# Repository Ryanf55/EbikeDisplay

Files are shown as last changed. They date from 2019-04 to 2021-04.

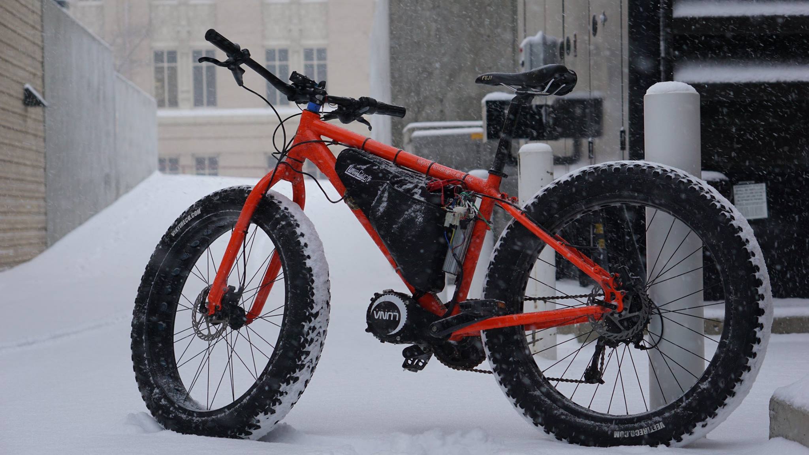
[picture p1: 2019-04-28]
Images/SnowyUse.jpg

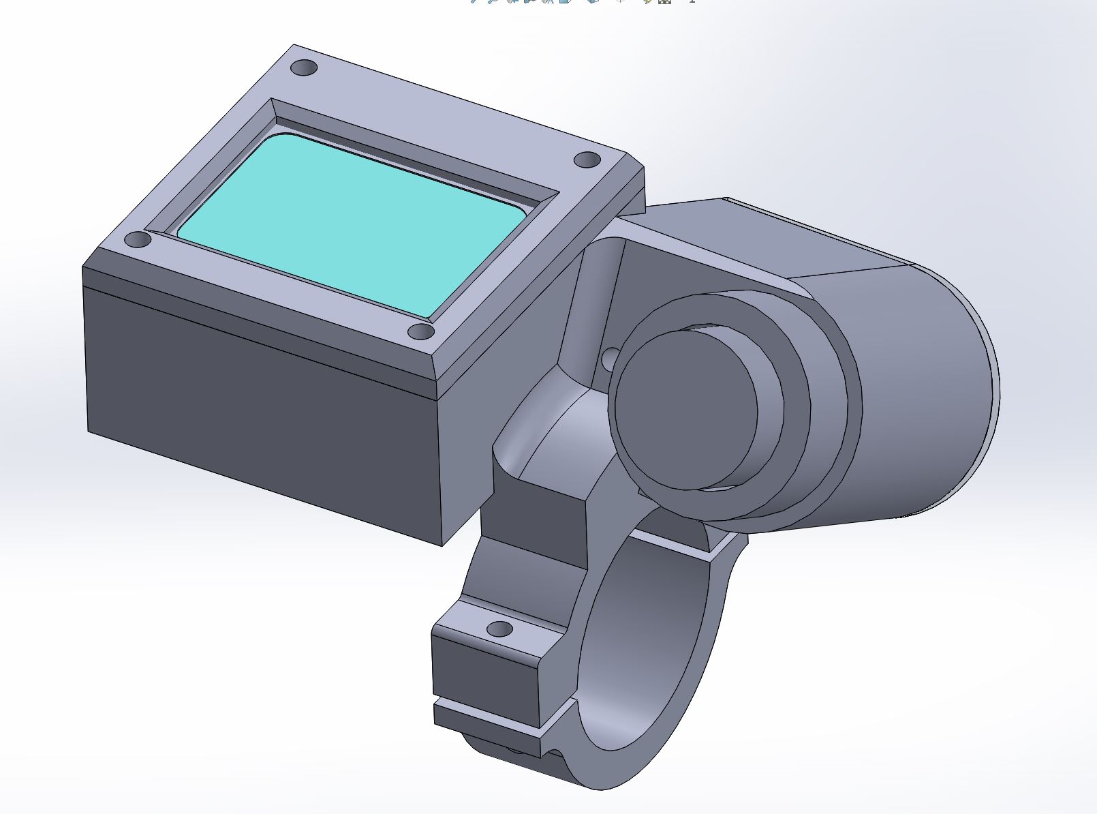
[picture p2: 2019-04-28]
Images/SW1.JPG

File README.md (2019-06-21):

This repo is for an Ebike Controller. It contains a PCB for Nokia 5110 LCD, SolidWorks files / STL's for the case, and Arduino code to work with a cyclone. 

Cyclone throttle cable pinout:
* blue - Vbat 
* black - gnd
* yellow- ignition (connect to Vbat to turn system on)
* green - throttle 0 to 3.3v

stock hall: D49E 503D

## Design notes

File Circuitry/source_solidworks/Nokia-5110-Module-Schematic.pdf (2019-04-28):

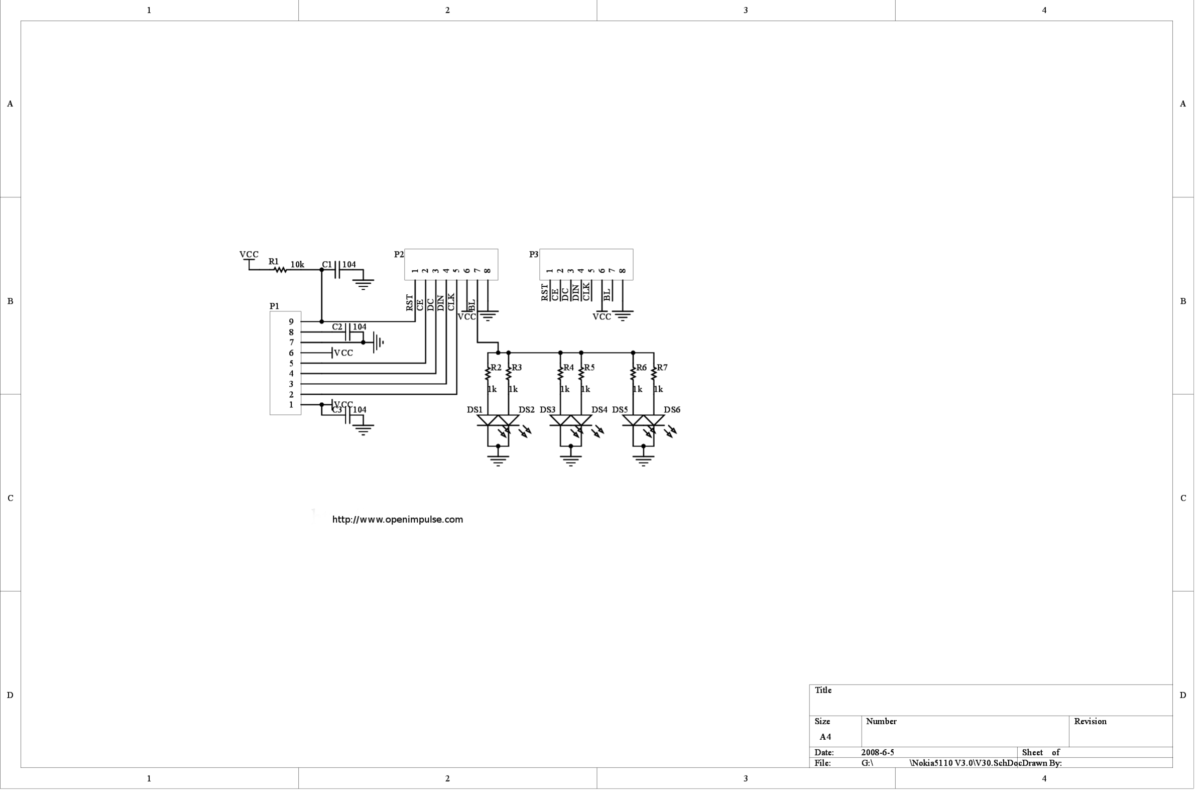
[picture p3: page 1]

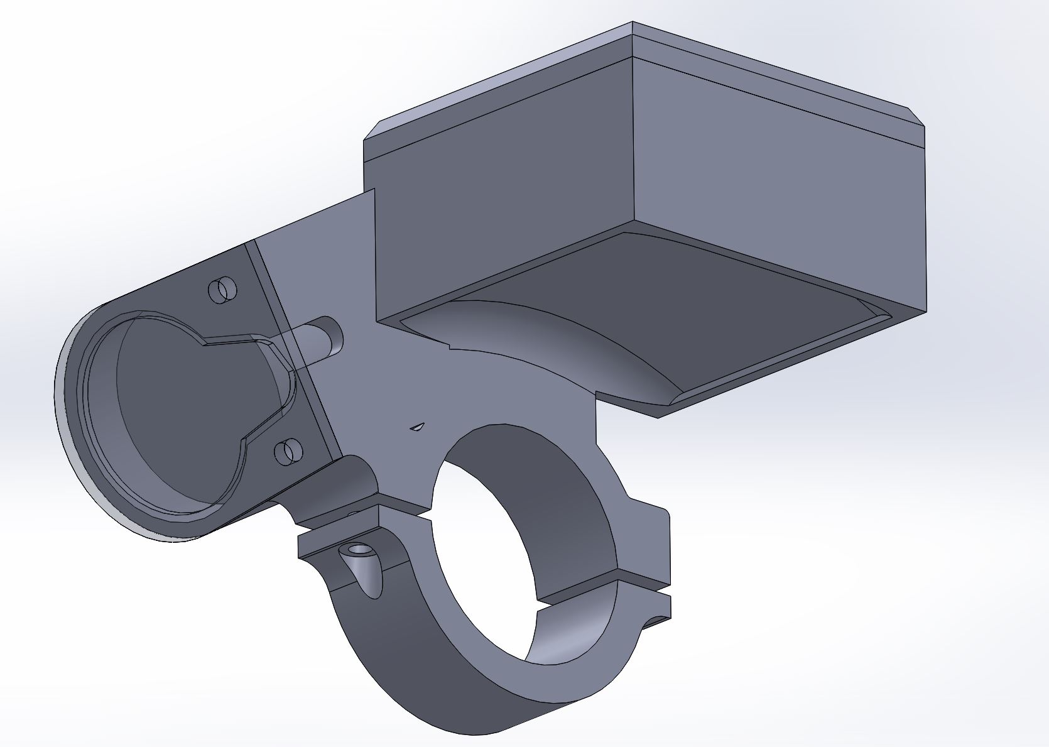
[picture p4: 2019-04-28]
Images/SW2.JPG

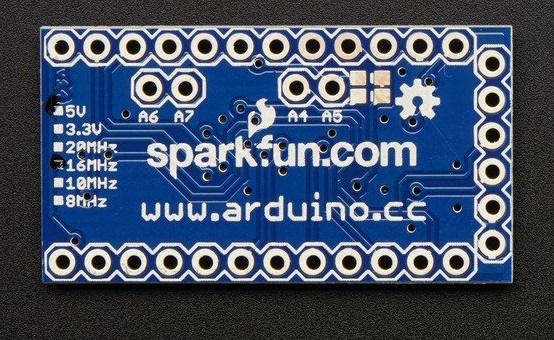
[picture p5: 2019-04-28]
Circuitry/arduino-pro-mini-1.snapshot.9/bot.jpg

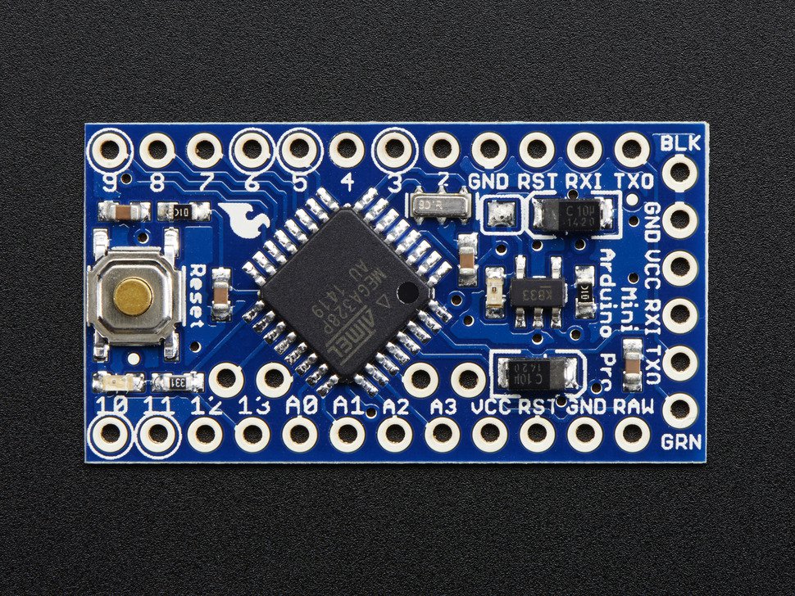
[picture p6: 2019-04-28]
Circuitry/arduino-pro-mini-1.snapshot.9/top.jpg

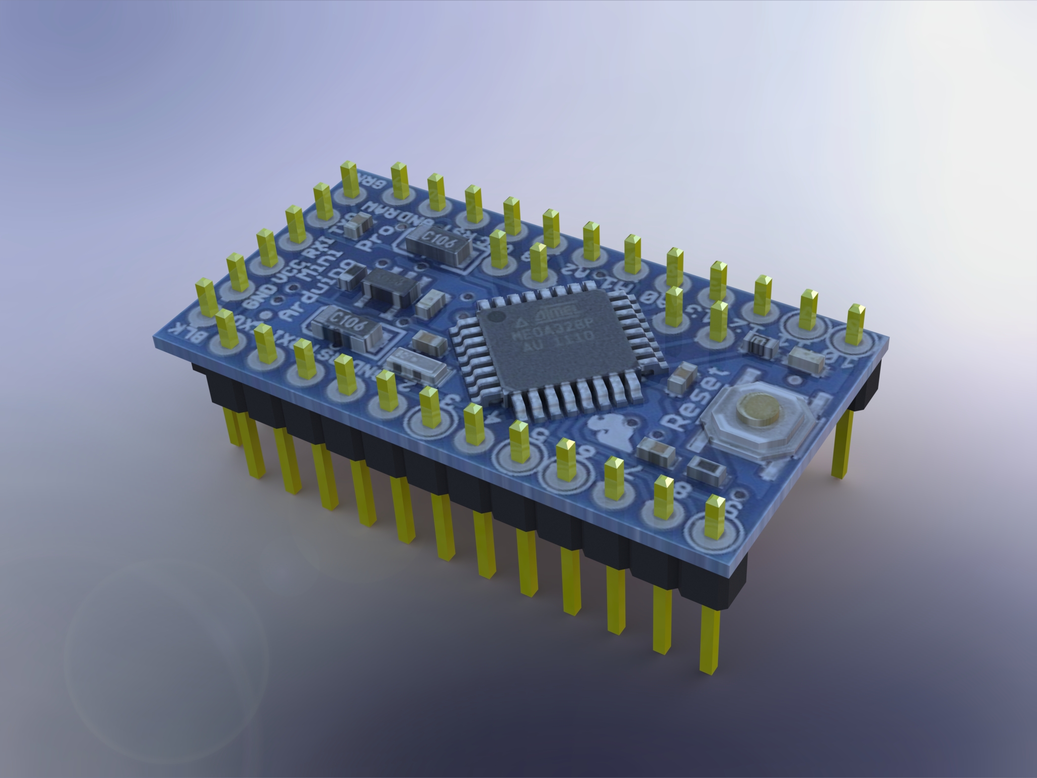
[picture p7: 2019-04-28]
Circuitry/arduino-pro-mini-1.snapshot.9/Renderings/Arduino_pro_mini.JPG

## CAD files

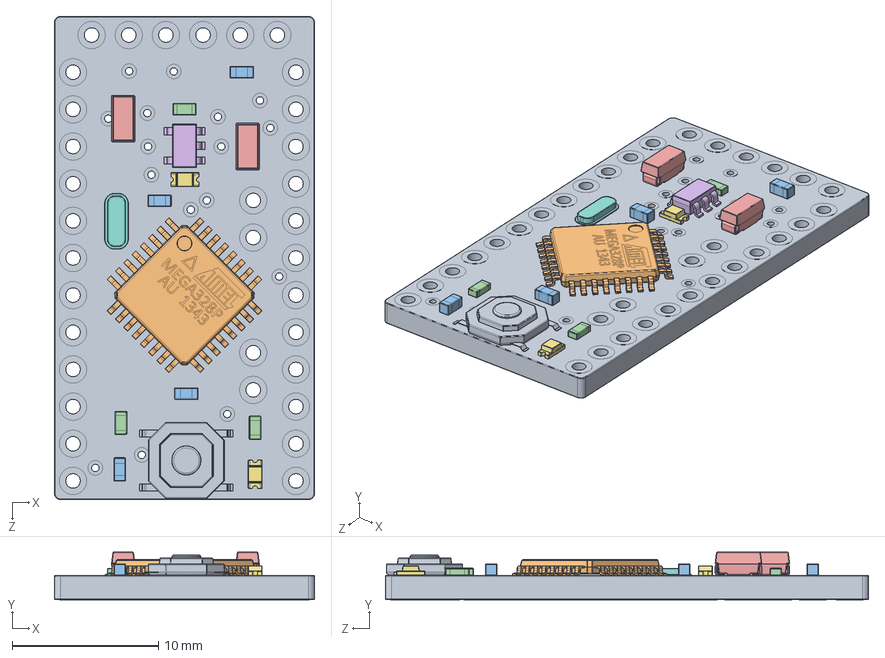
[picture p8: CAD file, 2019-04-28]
Circuitry/arduino-pro-mini-1.snapshot.9/ASSEMBLY.SLDASM
17.8 x 3.26 x 33.0 mm
board
ATmega
cap_603 x 4
res_603 x 3
condensateurTantale_106C x 2
SOT23-5
Surface Mount Chip LED 3.2x1.6mm x 2
TACTILE-SWITCH-SMD-ALT01

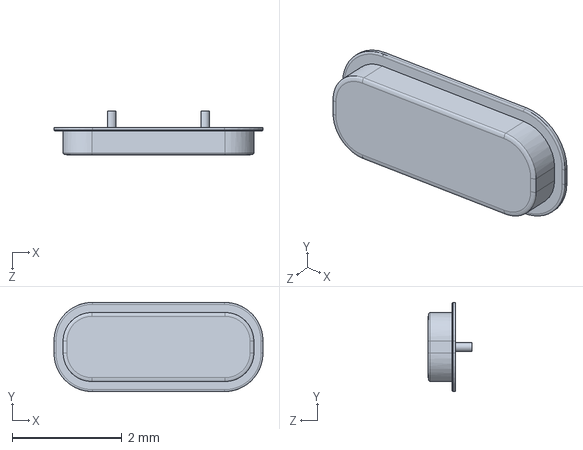
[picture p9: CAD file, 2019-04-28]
Circuitry/arduino-pro-mini-1.snapshot.9/Components/Crystal_Low_Profile.SLDASM
3.82 x 1.63 x 0.795 mm

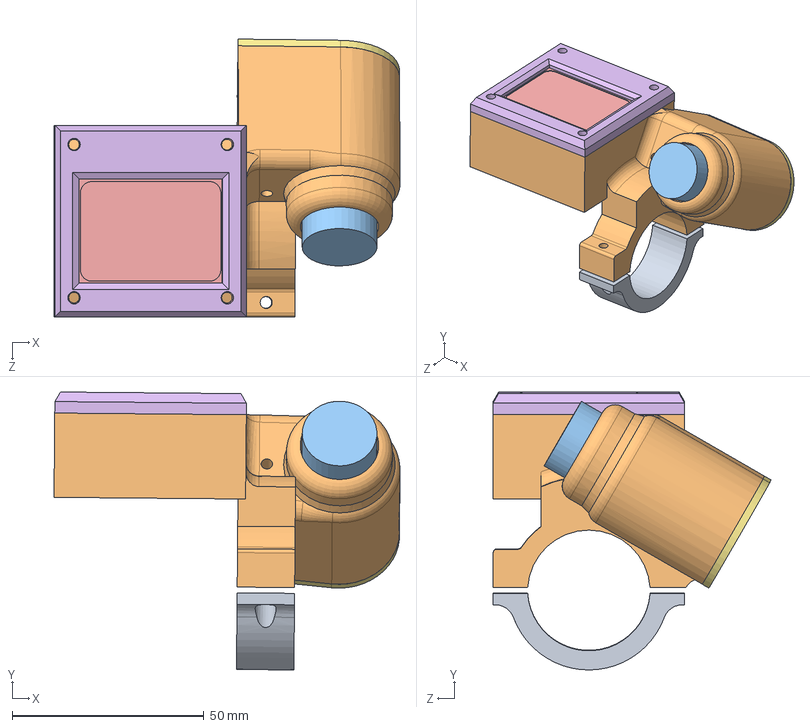
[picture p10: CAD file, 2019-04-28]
Mechanical/DisplayAssem.SLDASM
90.3 x 72.5 x 72.5 mm
displayRing
DisplayUpperRing
keyIgnition
board
displayCover
keyCover

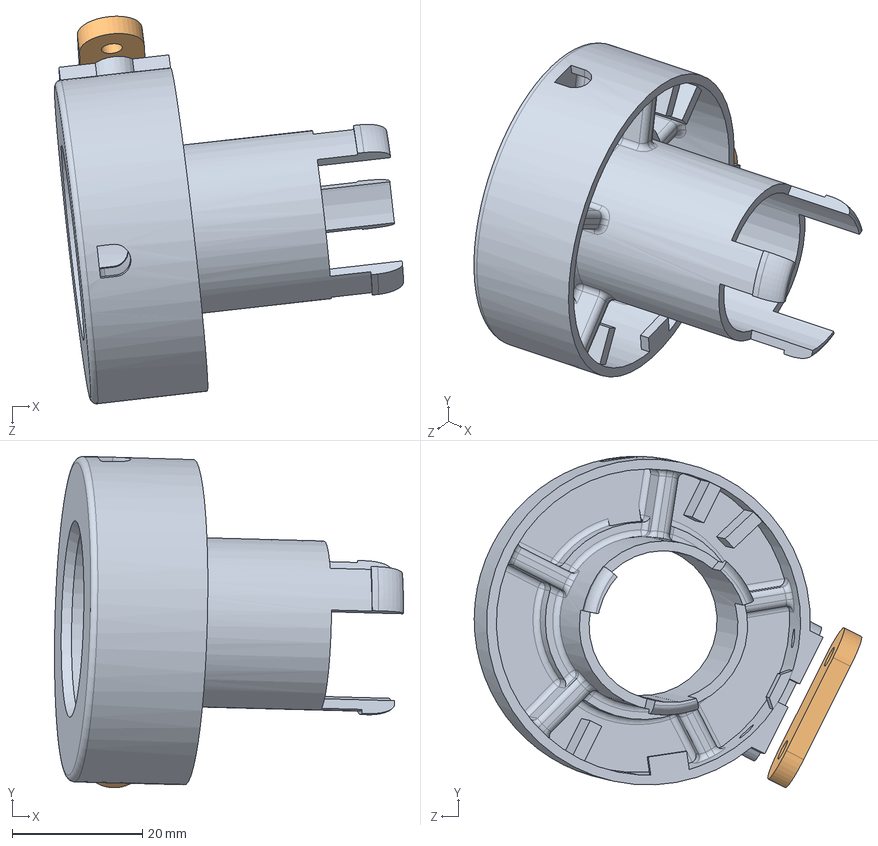
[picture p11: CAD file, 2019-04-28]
Mechanical/CycloneDisplayAssem.SLDASM
53.6 x 50.9 x 59.5 mm
DisplayMainBody
DisplaySensorTab

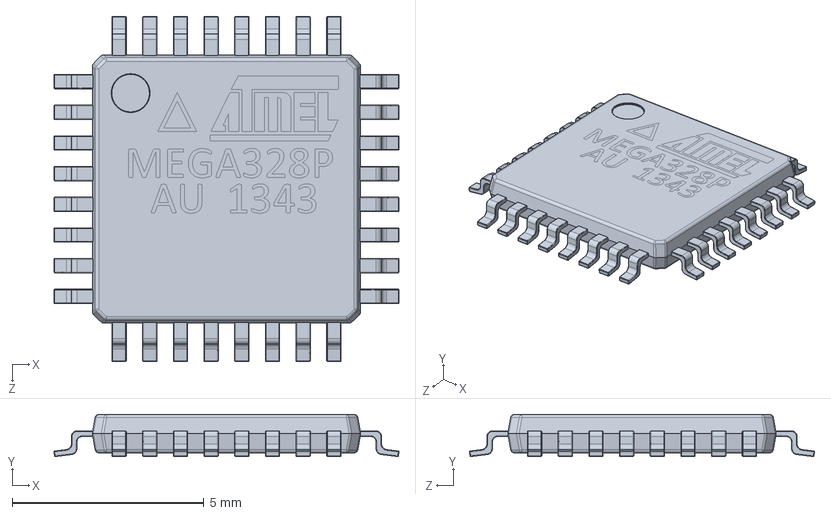
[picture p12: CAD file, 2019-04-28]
Circuitry/arduino-pro-mini-1.snapshot.9/Components/ATmega328 TQFP/ATmega.SLDPRT
9.00 x 1.10 x 9.00 mm

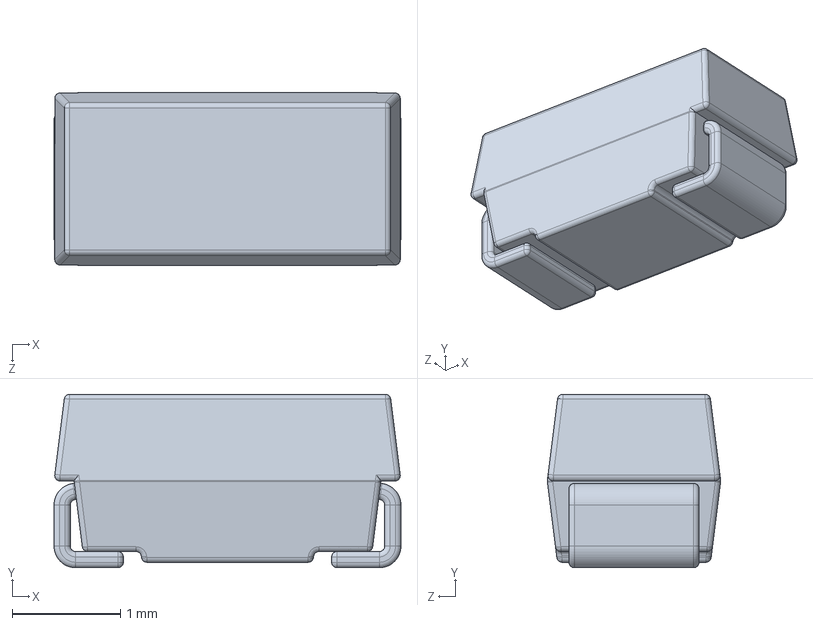
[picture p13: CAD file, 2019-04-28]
Circuitry/arduino-pro-mini-1.snapshot.9/Components/condensateurTantale_106C.SLDPRT
3.20 x 1.60 x 1.60 mm

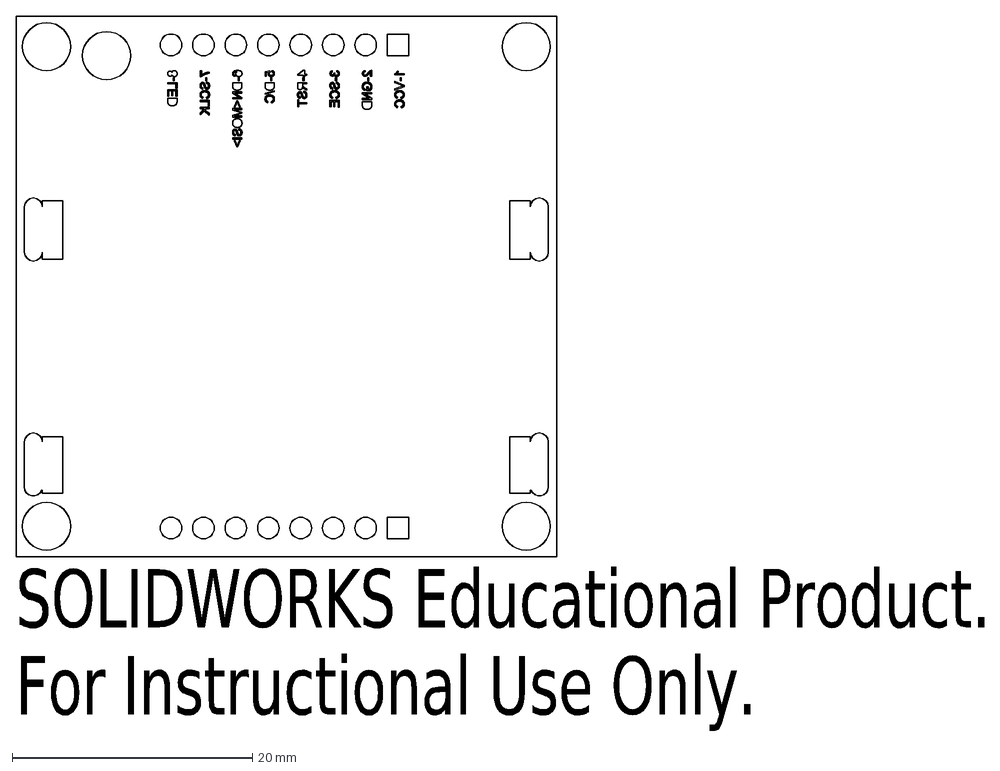
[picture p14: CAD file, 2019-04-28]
Circuitry/nokia.DXF
SOLIDWORKS Educational Product.
For Instructional Use Only.

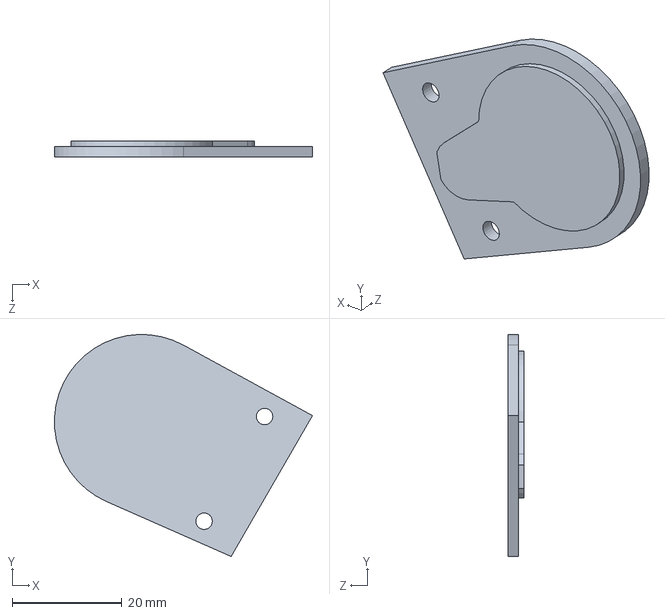
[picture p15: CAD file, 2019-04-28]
Mechanical/keyCover.SLDPRT
46.9 x 40.4 x 3.00 mm

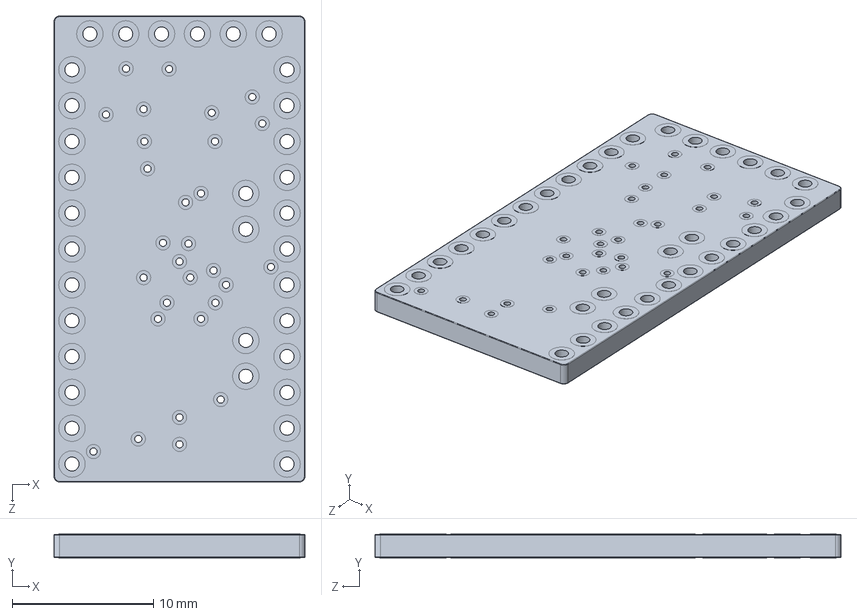
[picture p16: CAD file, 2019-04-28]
Circuitry/arduino-pro-mini-1.snapshot.9/board.SLDPRT
17.8 x 1.67 x 33.0 mm

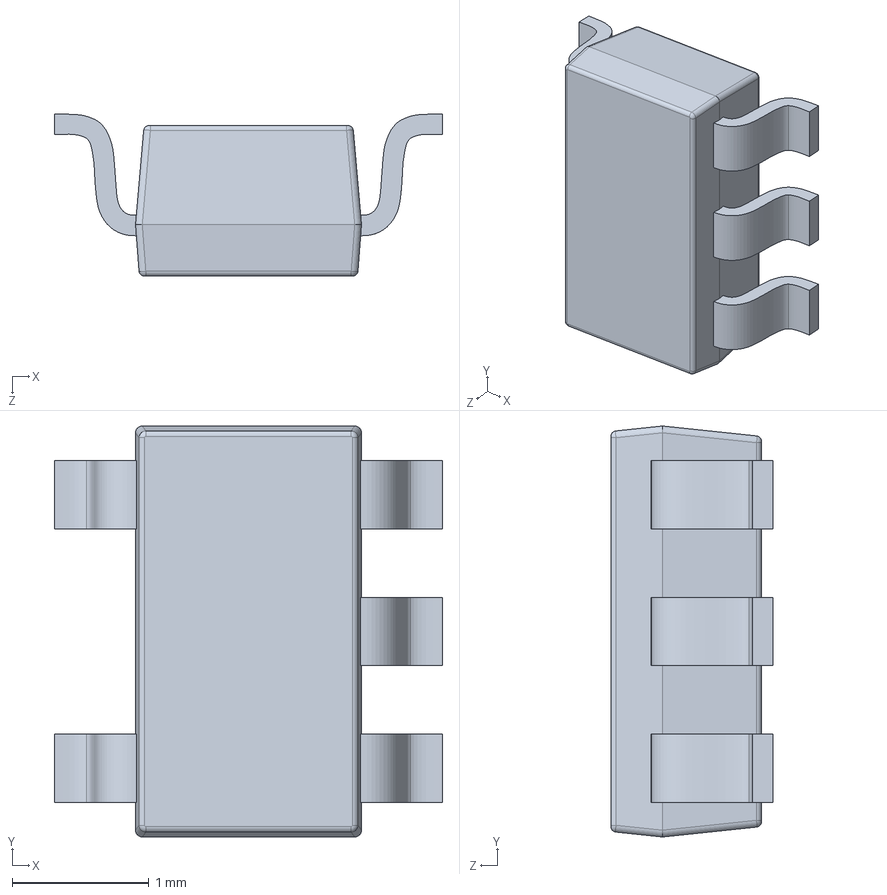
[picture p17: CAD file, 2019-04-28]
Circuitry/arduino-pro-mini-1.snapshot.9/Components/SOT23-5.SLDPRT
2.84 x 3.00 x 1.18 mm

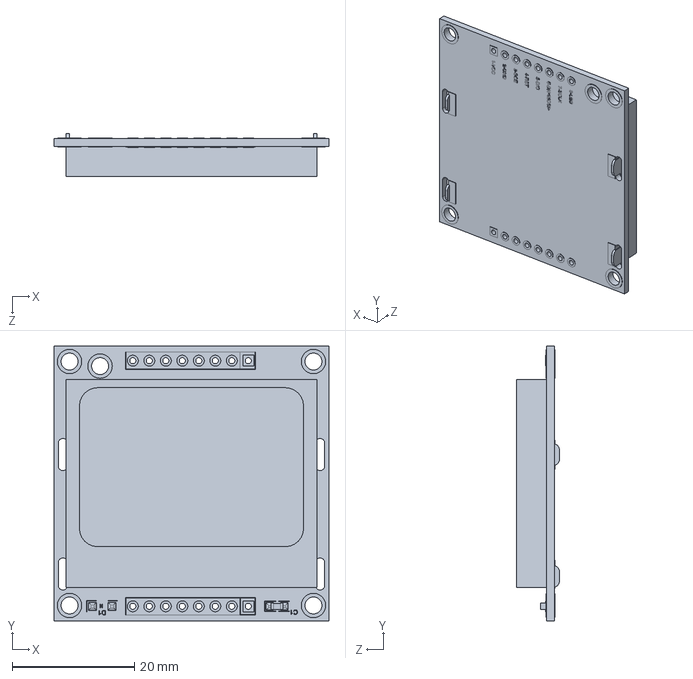
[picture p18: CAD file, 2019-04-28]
Circuitry/source_solidworks/products/10168/source_solidworks/Graphic LCD Nokia 5110.SLDPRT
45.0 x 45.0 x 7.02 mm

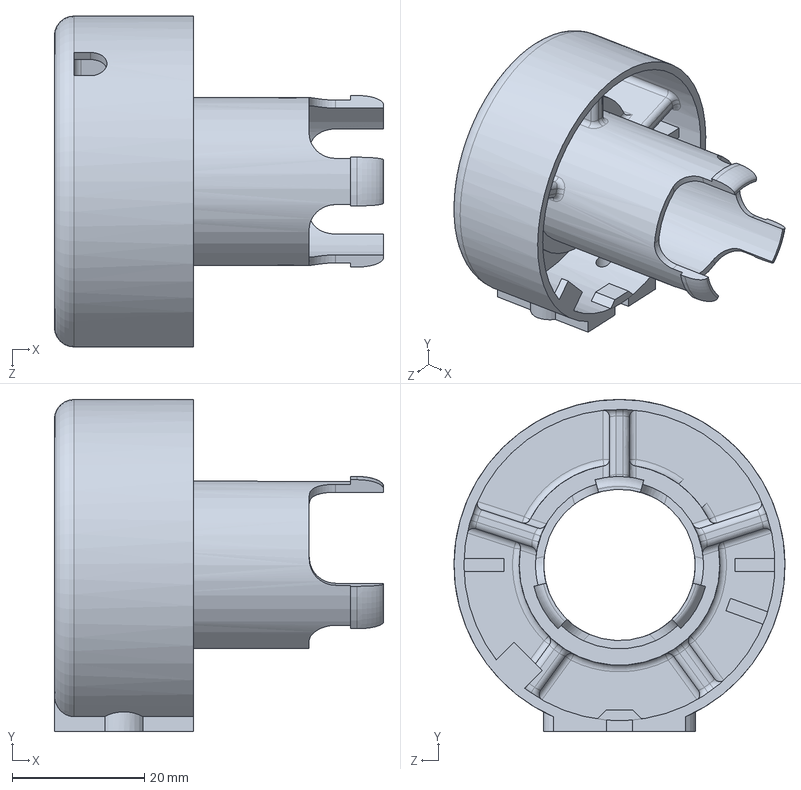
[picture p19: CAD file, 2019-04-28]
Mechanical/SensorBody.SLDPRT
49.8 x 50.2 x 50.0 mm

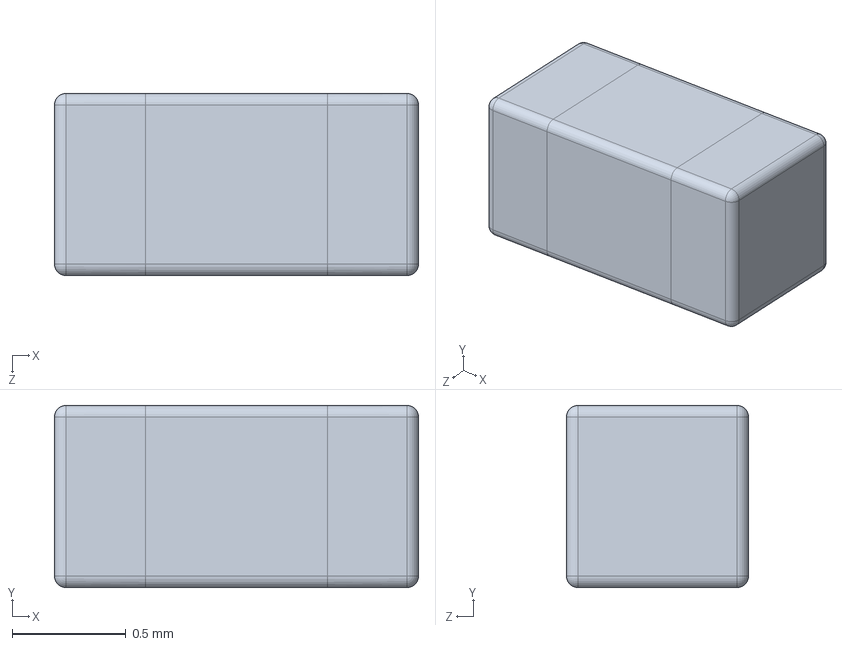
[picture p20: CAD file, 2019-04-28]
Circuitry/arduino-pro-mini-1.snapshot.9/Components/cap_603.SLDPRT
1.60 x 0.8 x 0.8 mm

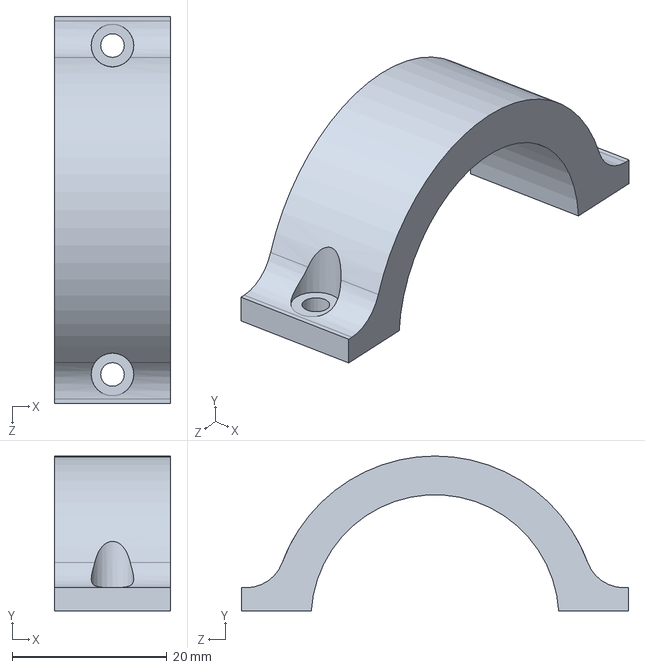
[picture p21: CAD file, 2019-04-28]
Mechanical/displayRing.SLDPRT
15.0 x 20.0 x 50.0 mm

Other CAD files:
Circuitry/arduino-pro-mini-1.snapshot.9/Components/Fusion001.sldprt
Mechanical/DisplaySensorTab.SLDPRT
Mechanical/displayCover.SLDPRT
Circuitry/arduino-pro-mini-1.snapshot.9/Components/Pin Header 1x12 TH Pitch 2.54mm.SLDPRT
Circuitry/arduino-pro-mini-1.snapshot.9/Components/Pin Header 1x2 TH Pitch 2.54mm.SLDPRT
Circuitry/arduino-pro-mini-1.snapshot.9/Components/Pin Header 1x6 TH Pitch 2.54mm.SLDPRT
Circuitry/arduino-pro-mini-1.snapshot.9/Components/Surface Mount Chip LED 3.2x1.6mm.SLDPRT
Circuitry/arduino-pro-mini-1.snapshot.9/Components/TACTILE-SWITCH-SMD-ALT01.SLDPRT
Circuitry/arduino-pro-mini-1.snapshot.9/Components/res_603.SLDPRT
Circuitry/arduino-pro-mini-1.snapshot.9/Components/solder.SLDPRT
Circuitry/arduino-pro-mini-1.snapshot.9/board.DXF
Circuitry/source_solidworks/10168.DXF
Circuitry/source_solidworks/products/10168/source_solidworks/10168.SLDPRT
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

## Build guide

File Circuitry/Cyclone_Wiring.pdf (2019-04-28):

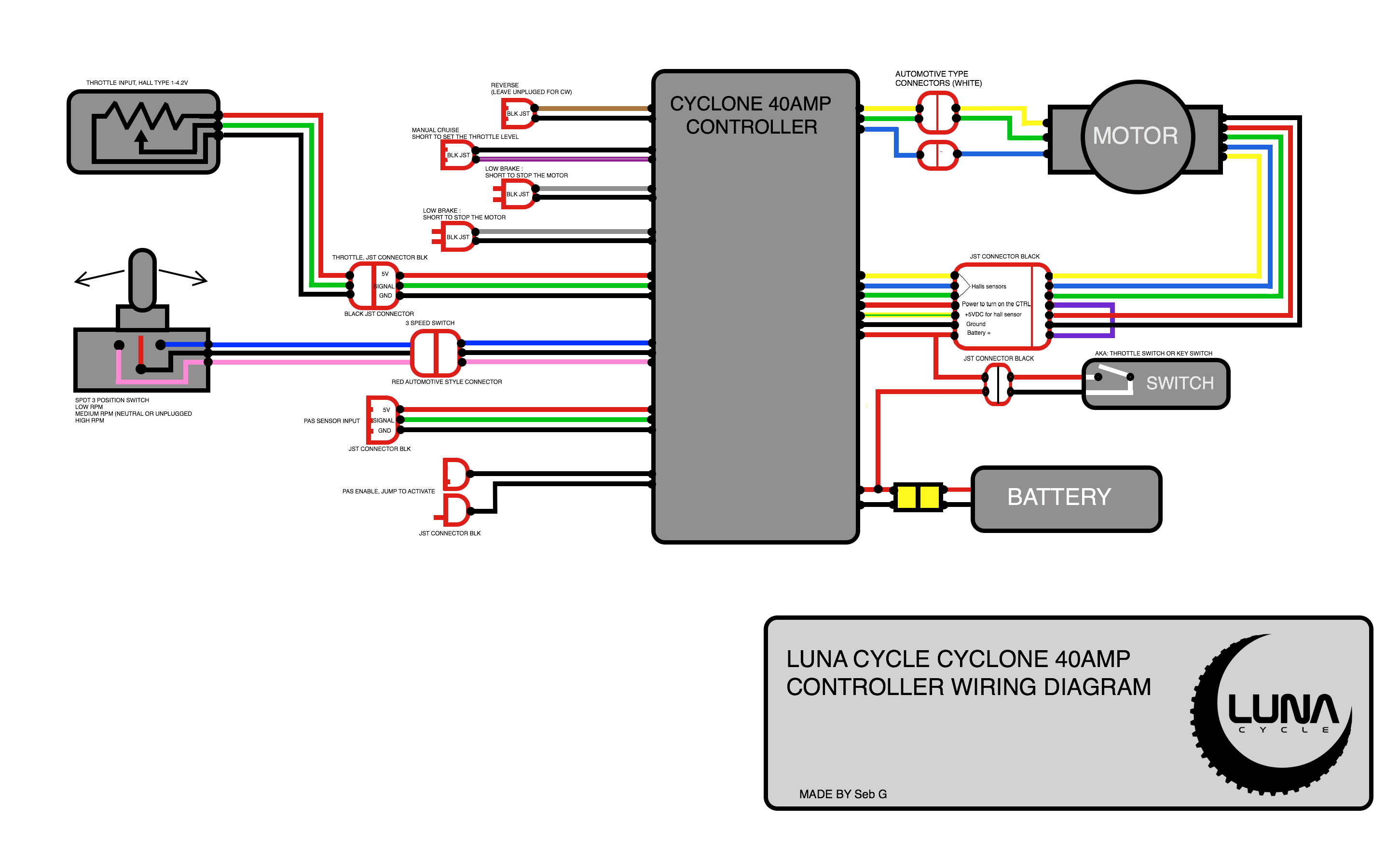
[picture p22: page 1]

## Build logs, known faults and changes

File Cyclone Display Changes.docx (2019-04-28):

Ebike Display/Controller

Ryan Friedman

Todo:

Increase ID of twist throttle by 0.35mm without increasing outer thickness, add large base fillet

Move light mount screws apart a tiny bit

Decrease key screw distance from key center axis by 0.5mm

Make key cover

Change LCD font size

Current electric bikes are subject to power limitations. In the US, E-bikes are limited to 750W. By installing a 3rd party motor and controller on a normal bike, this power requirement can be surpassed. However, many of the inexpensive kits are hard to install, aren’t tunable, and lack necessary features. The systems are not integrated, and while the sensors and data largely exist to improve the controller, none of the systems are designed to integrate well.

The goal of this project is to integrate the motor, speed controller, shifter, and throttle control into a single controller. User feedback will be provided via a screen, and configuration will be possible either through a menu on the screen, phone application utilizing a USB OTG cable, or a laptop with program.

Specifically, the Cyclone motor and half-twist throttle, sold by Luna cycle, are the centerpiece of the hardware. At a high level, the twist throttle contains a key ignition to turn on the controller. The throttle sends an analog voltage to the motor, which is proportional to the speed. The throttle also features a dim LED indicator for the voltage, but it is not accurate. Another downside is that the key ignition is in the way of the rear shifter, so the rider needs to remove their hand from the bars to shift.

By communicating with the speed controller, reading the raw throttle values, and commanding the shifting, a current-based PID control can be implemented to provide a smoother and more natural motor response. More useful data metrics can be supplied to the rider via a new display, and electronic shifting will aid the motor in achieving optimum efficiency and RPM if implemented. Safety can be improved by preventing large increases in motor speed at low riding speed. Safety will also be improved through current limits, a minimum battery voltage, and increased waterproofing of the electronics.

- Physical
  - Water Resistant
  - Improve Ergonomics of twist throttle
    - Move key ignition to above the brake
  - Add-on lights
    - Front lights, adjustable brightness via PWM
    - Maybe multicolor?
- Electrical
  - Adjust speed line
    - Smooth from quick changes
    - Add expo to make low end more sensitive
  - Bright Voltage Display
  - 3 button interface
    - Up, down, select(short)&(long)
- Parts:
  - 3D printed case
  - M3 screws
  - Light 3D print mounts
  - Circuity main components:
    - Nokia Display
    - 3 nav buttons, emergency stop
    - 72V voltage regulator
    - Buzzer
  - Extensions
    - Lights
    - Servo shifting
      - Servo
      - 3D printed cable holder
      - Large tactile buttons
      - motor speed crawl when shifting?
    - Brake cutoff?

References:

Ebike Parts:

Voltage reg: Max5035

https://datasheets.maximintegrated.com/en/ds/MAX5035.pdf

-> Needs application circuit shown

https://www.digikey.com/products/en/integrated-circuits-ics/pmic-voltage-regulators-dc-dc-switching-regulators/739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

Nokia 5110 image:

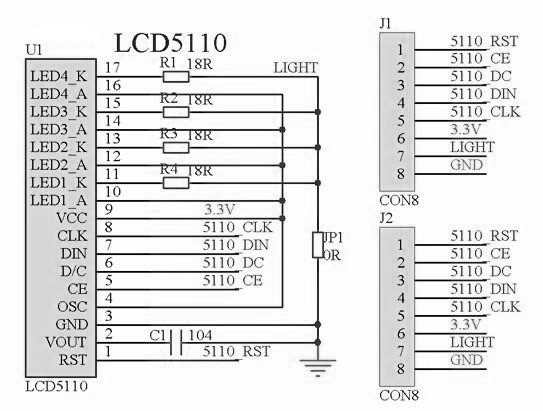
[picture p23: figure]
Image result for nokia 5110 schematic

- Add balance pot to adjust light, or a jumper

Source for adding Arduino shield:

https://www.youtube.com/watch?v=9KQxZM6MeHA

Current Sensing:

Current sense IC: INA 169 (high side) or INA 199 (low side)

http://www.ti.com/product/INA199/technicaldocuments

Note: Using INA 2xx series with 16 bit ADC may result in best PID performance at expense of increased cost.

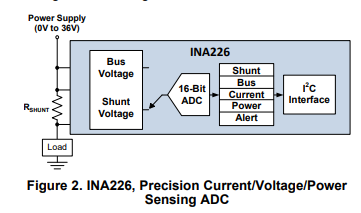
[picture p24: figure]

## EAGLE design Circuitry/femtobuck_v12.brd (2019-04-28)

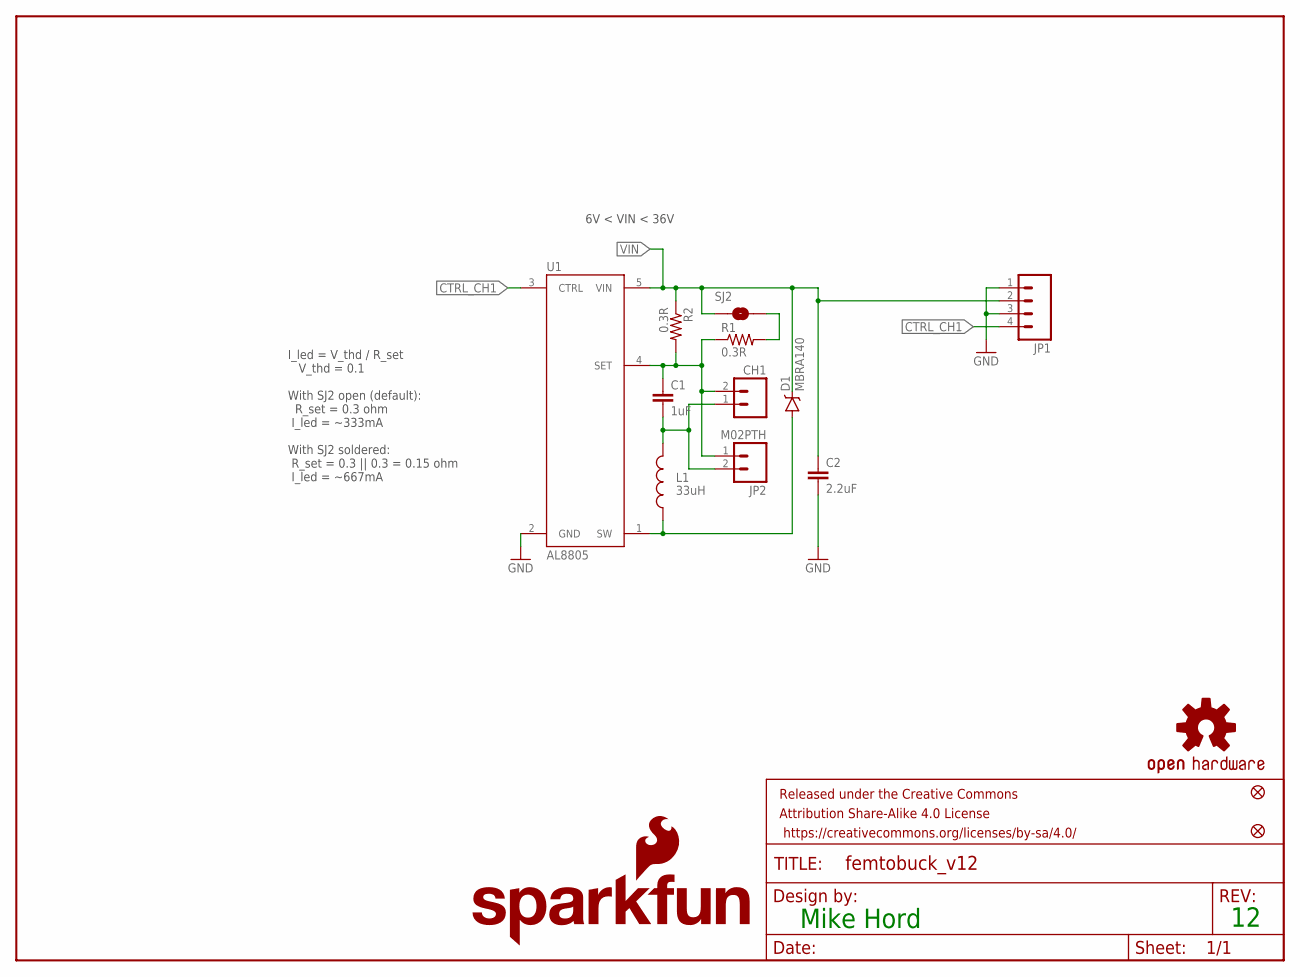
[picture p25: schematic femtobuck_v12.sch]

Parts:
C1: 1uF; 1206-CAP
C2: 2.2uF; 1206-CAP
CH1: M023.5MM_LOCK; SCREWTERMINAL-3.5MM-2_LOCK
D1: MBRA140; SMA-DIODE
FID1, FID2: FIDUCIAL1X2; FIDUCIAL-1X2
FRAME1: FRAME-LETTER; CREATIVE_COMMONS
JP1: M04PTH; 1X04
JP2: M02PTH; 1X02
L1: 33uH; SRN6045
LOGO1: OSHW-LOGOS; OSHW-LOGO-S
LOGO2: SFE_LOGO_NAME_FLAME.1_INCH; SFE_LOGO_NAME_FLAME_.1
R1, R2: 0.3R; 0805
SJ2: NO Jumper; PAD-JUMPER-2-NO_NO_SILK
U1: AL8805; SOT23-5

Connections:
CTRL_CH1: JP1.4, U1.3 (CTRL)
GND: C2.2, JP1.1, JP1.3, U1.2 (GND)
unnamed: R1.2, SJ2.2
OUT+: C1.1, CH1.2, JP2.1, R1.1, R2.2, U1.4 (SET)
OUT-: C1.2, CH1.1, JP2.2, L1.2
SW: D1.A, L1.1, U1.1 (SW)
VIN: C2.1, D1.C, JP1.2, R2.1, SJ2.1, U1.5 (VIN)

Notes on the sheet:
I_led = V_thd / R_set V_thd = 0.1 With SJ2 open (default): R_set = 0.3 ohm I_led = ~333mA With SJ2 soldered: R_set = 0.3 || 0.3 = 0.15 ohm I_led = ~667mA
Mike Hord
6V < VIN < 36V

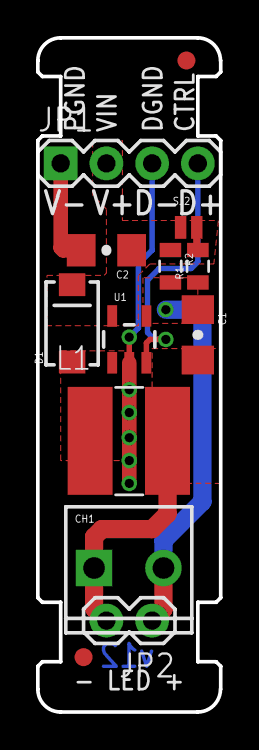
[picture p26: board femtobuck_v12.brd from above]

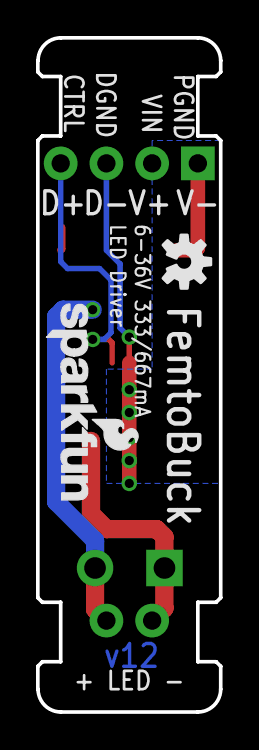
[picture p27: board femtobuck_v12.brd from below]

Board: 2 copper layers, 10.2 x 37.5 mm, 16 parts (2 on the bottom side), 7 nets.

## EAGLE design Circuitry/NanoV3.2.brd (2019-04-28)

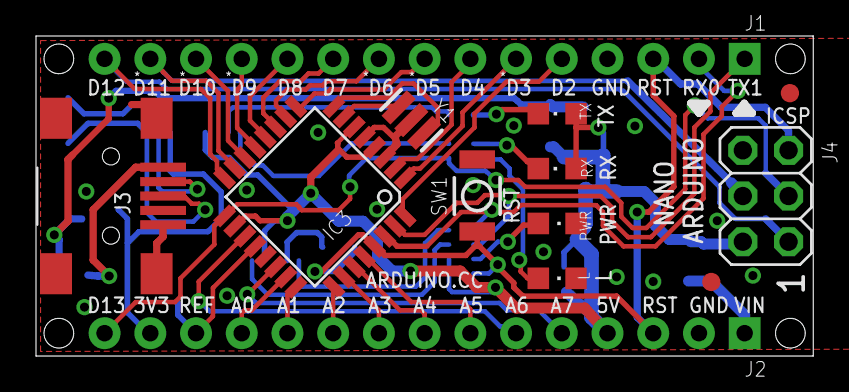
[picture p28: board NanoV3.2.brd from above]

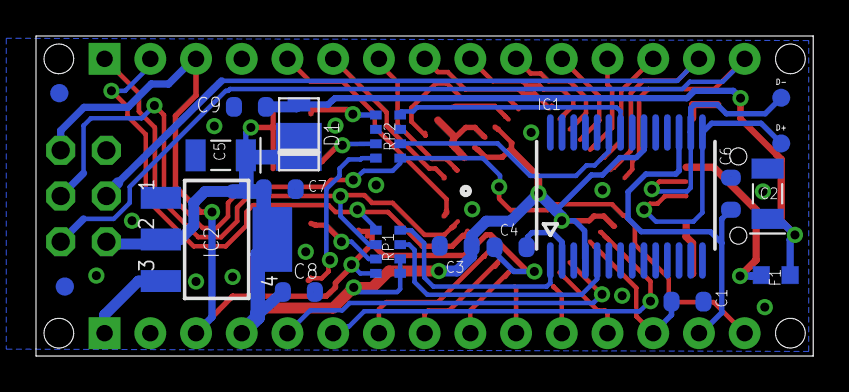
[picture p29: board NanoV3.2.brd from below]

Board: 2 copper layers, 43.2 x 17.8 mm, 33 parts (17 on the bottom side), 43 nets.

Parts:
C1, C4, C6, C9: 100nF; C0603-ROUND
C2, C5: 4,7uF_16V; TAN-A
C3, C7, C8: 1uF; C0603-ROUND
D1: SS1P3L; DO220AAL
D+: DNP; TP-1.00MM
D-: DNP; TP-1.00MM
F1: MFFSMF050; 0603-1608X90N
FRAME1: DNP; FRAME
IC1: FT232RL; SSOP28
IC2: LM1117IMPX-5.0; LINEAR_SOT223
IC3: ATMEGA328P-AU; TQFP32-08
J1, J2: XXXX_STRIPNANO; HEAD15-NOSS
J3: USB-MINI-B_2
J4: 2X03
L: Yellow; CHIPLED_0805
PWR: Green; CHIPLED_0805
RP1, RP2: 1K; CAY16
RX: Red; CHIPLED_0805
SW1: RESET; SMD_157SW
TX: Green; CHIPLED_0805
U$4, U$5, U$53, U$54: DNP; FD-1-1.5
Y1: 16MHz; RESONATOR

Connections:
3V3: C6.2, IC1.17, J2.14
+5V: C3.1, C5.1, C7.1, C8.1, D1.P$1, IC1.4, IC1.20, IC2.2, IC2.4, IC3.4, IC3.6, IC3.18, J2.4, J4.2, RP1.5, RP1.6, RX.A, TX.A
A0: IC3.23, J2.12
A1: IC3.24, J2.11
A2: IC3.25, J2.10
A3: IC3.26, J2.9
A4: IC3.27, J2.8
A5: IC3.28, J2.7
A6: IC3.19, J2.6
A7: IC3.22, J2.5
AREF: C1.1, IC3.20, J2.13
COM: C1.2, C2.2, C3.2, C5.2, C6.1, C7.2, C8.2, C9.2, IC1.7, IC1.18, IC1.21, IC1.25, IC1.26, IC2.1, IC3.3, IC3.5, IC3.21, J1.4, J2.2, J3.1, J3.6, J3.7, J3.8, J3.9, J4.6, L.C, PWR.C, RP2.3, RP2.6, SW1.1, Y1.2
D0/RX: IC3.30, J1.2, RP1.1
D1/TX: IC3.31, J1.1, RP1.2
D2: IC3.32, J1.5
D3: IC3.1, J1.6
D4: IC3.2, J1.7
D5: IC3.9, J1.8
D6: IC3.10, J1.9
D7: IC3.11, J1.10
D8: IC3.12, J1.11
D9: IC3.13, J1.12
D10: IC3.14, J1.13
D11/MOSI: IC3.15, J1.14, J4.4
D12/MISO: IC3.16, J1.15, J4.1
D13/SCK: IC3.17, J2.15, J4.3, RP2.1
unnamed: IC3.8, Y1.3
unnamed: IC3.7, Y1.1
unnamed: PWR.A, RP1.3
unnamed: C4.2, IC1.2
unnamed: D+.X, IC1.15, J3.3
unnamed: D-.X, IC1.16, J3.4
unnamed: L.A, RP2.8
unnamed: IC1.23, RP2.2
unnamed: IC1.22, RP2.4
unnamed: RP2.5, TX.C
unnamed: F1.2, J3.5
unnamed: RP2.7, RX.C
RESET: C4.1, IC3.29, J1.3, J2.3, J4.5, RP1.4, SW1.2
RX: IC1.1, RP1.8
TX: IC1.5, RP1.7
VIN: IC2.3, J2.1
VUSB: C2.1, C9.1, D1.P$2, F1.1

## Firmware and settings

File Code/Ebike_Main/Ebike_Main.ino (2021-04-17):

//Electric Bike Controller for Cyclone
//Ryan Friedman
//1-10-2019

/*
 * Todo:
 * Change display font size for voltage
 * Speed sensor
 * Write engine for data display (Struct of name -  value -  unitText). Only print units and lines when menu is changed. 
 *  Struct is made
 *  Need to write getters and setters
 * Write engine for datalines
 * Write engine for 1 button scrolling
 * Link up parameters with data display struct
 * 
 * */

#define LARGE_FONT u8g2_font_profont17_tf
#define MEDIUM_FONT u8g2_font_profont15_tf
#define SMALL_FONT u8g2_font_profont12_tf


//Voltage input: 12V via stepdown from power wire into RAW

//Pins ****************************************************************************************
#define THR_IN_PIN 0 //A0,
#define THR_OUT_PIN 6 //PWM pin, labeled 6
#define BATT_PIN 1 //A1


//Throttle constants. Input constants should be less range than the sensor values, so they get coerced to the same range always, with some deadband. 
//The output constants should be larger range than the cycle expects to achieve full range. 
//Most important, do not raise thrOutMin too high, or the motor will always run. 
#define thrInMin  51 //min throttle, no speed
#define thrInMax  75 //max throttle, high speed
#define thrOutMin 20 //min speed motor, motor turns on @ ~25 so leave it ~20
#define thrOutMax 100 //max speed motor
#define ALPHA 0.10 //alpha for expo filter, between 0 and 1. If alpha is 1, weights latest sample only, whereas low alpha smooths a lot

//Voltages *********************
#define VOLT_ARDUINO 3.3 //arduino 5V or 3.3V
#define BAT_CELLS 14
#define VPC_MAX 4.2 // volts per cell, max for li-ion
#define VPC_MIN 3.6 // volts per cell, min for li-ion
#define VOLT_MAX (VPC_MAX * BAT_CELLS)
#define VOLT_MIN (VPC_MIN * BAT_CELLS)


//Display *********************************************************************************
#include <U8g2lib.h>

#ifdef U8X8_HAVE_HW_SPI
#include <SPI.h>
#endif
#ifdef U8X8_HAVE_HW_I2C
#include <Wire.h>
#endif

// U8g2 Contructor List (Picture Loop Page Buffer)
// The complete list is available here: https://github.com/olikraus/u8g2/wiki/u8g2setupcpp
// Please update the pin numbers according to your setup. Use U8X8_PIN_NONE if the reset pin is not connected

U8G2_PCD8544_84X48_1_4W_SW_SPI u8g2(U8G2_R2, /* clock (SCLK)=*/ 13, /* data (DN(MOSI))=*/ 11, /* cs (SCE) =*/ 10, /* dc (D/C)=*/ 9, /* reset (RST)=*/ 8);  // Nokia 5110 Display
//U8G2_PCD8544_84X48_1_4W_HW_SPI u8g2(U8G2_R0, /* cs=*/ 10, /* dc=*/ 9, /* reset=*/ 8);           // Nokia 5110 Display





void draw(
  byte pageNum,
  float main_voltage,
  float thrHallPer,
  float aout,
  float thrFiltered,
  float battPercent
  ) 
{
 
  u8g2.firstPage();
  do 
  {

    
    if (pageNum == 1) 
    { //draw voltage and current
//      u8g2.setFont(LARGE_FONT);
//      u8g2.setCursor(0,17);
//      u8g2.print(main_voltage);
//      u8g2.setFont(SMALL_FONT);
//      u8g2.print("vb/");
//      u8g2.print(VOLT_MAX);
//
//      u8g2.setFont(MEDIUM_FONT);
//      u8g2.setCursor(0,25);
//      u8g2.print(thrHallPer);
//      u8g2.setFont(SMALL_FONT);
//      u8g2.print("thrHall");
//
//      u8g2.setFont(SMALL_FONT);
//      u8g2.setCursor(0,37);
//      u8g2.print(aout);
//      u8g2.setFont(SMALL_FONT);
//      u8g2.print("vo");
//
//      u8g2.setFont(SMALL_FONT);
//      u8g2.setCursor(0,49);
//      u8g2.print(thrFiltered);
//      u8g2.setFont(SMALL_FONT);
//      u8g2.print("vfilter");

        u8g2.setFont(LARGE_FONT);
        u8g2.setCursor(0,17);
        u8g2.print(battPercent);
        u8g2.setFont(SMALL_FONT);
        u8g2.print("%");

        u8g2.setFont(MEDIUM_FONT);
        u8g2.setCursor(0,30);
        u8g2.print(main_voltage);
        u8g2.setFont(SMALL_FONT);
        u8g2.print("v");
    }
    else 
    {
      u8g2.setFont(u8g2_font_profont12_tf);
      u8g2.drawStr(0,8,"Page Num");
      u8g2.drawStr(0,17,"Error");
    }
    
    
   
   
  } while ( u8g2.nextPage() );
  
}



float prevThrOut = 0;

int adjustThr(float rawVal) 
{
  //Map input to output (negative slope)
  float slope = (thrOutMin - thrOutMax) / (thrInMin - thrInMax);
  float outVal =  slope*(rawVal - thrInMin) + thrOutMin;
  if (outVal < thrOutMin)  //no use sending out signals lower than minThrottle
    return thrOutMin;
  else if (outVal > thrOutMax) //overflow of expected max speed command will stop the motor. 
    return thrOutMax;
  else
  return outVal;
  return -1;
}


int expoThr(float new_sample, float ma_old){
  if (new_sample < ma_old)
  {
    return new_sample;
  } else 
  {
    return ALPHA * new_sample + (1-ALPHA) * ma_old;
  }
}
  

float calcVoltage(float v)
{
  //multiplier = 21.2 (Calibated)
  return v*22.85*VOLT_ARDUINO/1023.0;
}

float calcPercentage(float batVolt)
{
  return 100 / (VOLT_MAX - VOLT_MIN) * (batVolt - VOLT_MIN);
}




void setup() 
{
  
  u8g2.begin(); //Start Display
  u8g2.setContrast(135);
}

float thr_old = thrOutMin;
void loop() 
{

  //Calculate Sensor Values
  float thrHallPer= analogRead(THR_IN_PIN) * (100.0 / 1023.0);
  // 43 low throttle, 78 high throttle
  float battVoltage = calcVoltage(analogRead(BATT_PIN)) ;
  int scaledThrottlePer = adjustThr(thrHallPer);
  thr_old = expoThr(scaledThrottlePer, thr_old);
  
 
  analogWrite(THR_OUT_PIN,((int)thr_old*2.55));
//  prevThrOut = 0.75*prevThrOut + 0.25*scaledThrottlePer;
//
//  //Update Display
//  //dispPage1(battVoltage,thrHallPer,prevThrOut);

//  
  delay(50);  
  draw(1, battVoltage, (int)thrHallPer, scaledThrottlePer, (int)thr_old, calcPercentage(battVoltage));
}

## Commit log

2019-06-21 add throttle pinout for cyclone
2021-04-02 Modify to support correct pins
    * Correct bug in throttle conversion from hall to output
    * Add expo filtering on output throttle signal
    * Add conversion to battery percentage
    [Ebike_Main.ino]
2021-04-17 Fix calibration value for voltage
    [Ebike_Main.ino]

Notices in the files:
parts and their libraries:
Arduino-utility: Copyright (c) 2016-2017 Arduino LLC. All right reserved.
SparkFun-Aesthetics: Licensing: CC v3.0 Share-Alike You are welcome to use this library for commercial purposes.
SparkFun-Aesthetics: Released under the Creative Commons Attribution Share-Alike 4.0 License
